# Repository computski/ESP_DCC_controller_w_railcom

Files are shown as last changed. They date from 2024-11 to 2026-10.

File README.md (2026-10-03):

# ESP_DCC_controller_w_railcom
PRODUCTION 2026-10-03. ESP 8266 DCC controller with railcom support. Uses most of the codebase from the ESP_DCC_controller project, but this project additionally supports a railcom cutout on the controller i.e. takes both X and Y to ground (or both 12v) during a railcom cutout slot that appears after every loco packet sent to line.   A railcom decoder will assert its data during the railcom cutout, and this is detected by dedicated hardware based around an LM319.  This data is fed to the ESP hardware UART and is gated-in during the cutout period via a railcom sync signal to a 6n317 opto isolator.  The UART operates at 250kbs.  I have designed a custom PCB for this project.

Now moved to ArduinoJson v7.0.4
Now uses ESPAsyncWebserver

https://arduinojson.org/news/2024/01/03/arduinojson-7/

Note: RX pin input is idle high.   The same is true of the comparator, i.e. active is a low signal

The railcom detector is integrated into the controller.  It uses an adaptation of the reference circuit in NRMA doc s-9.3.2_2012.   This is a floating earth detector based on the LM319.  The LM319 can operate from 
a split power rail, which means it does not use the negative rail to drive the opto LED current, instead driving the LED from the +ve rail and into the floating earth.  The LM319 is also faster than the LM393.
A high speed (10Mbd) 6N137 opto isolator is used to level shift between the floating earth and the RX input on the ESP mini, and is also used as a gate-in filter.
The 6N137 has an open collector output buffer and this is ideal as we can wire-OR this into the RX pin along with the on-board ESP mini USB-serial circuitry; this has an on-board 400R pull up.

The 6N137 also has a gating input on the output stage, and we drive this from railcom sync which is active high during the cutout.  This greatly cuts down on junk data into the UART and reduces software workload.

2025-05-13 fixed a bug in global.h which incorrectly defined the drive pins for the 2-pin drive arrangement on the LMD18200.  Railcom detector now works properly and with loco facing in either direction.

2026-02-19 LocoNet working, added support for OPC_IMM dcc immediate messages which allows use of multi aspect signals

2026-04-05 LocoNet bidirectional messages to Panel Pro working, additionally support for ESPACC accessory controller on the WiThrottle port

2026-10-03 final fixes to revised html pages in data

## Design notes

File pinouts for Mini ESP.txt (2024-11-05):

GPIO16 D0 jog SW (pcb pull down)
GPIO5  D1 Jog CK (pcb pull up)
GPIO4  D2 Jog DT (pcb pull up)
GPIO0  D3 SDA
GPIO2  D4 SCL
GPIO14 D5 IN2 IN4 LMD-DIR
GPIO12 D6 IN1 IN3 
GPIO13 D7 ENA+B LMD-PWM
GPIO15 D8 to JP2 presumably eStop to gnd
A0 goes to sense
GPIO3 RX

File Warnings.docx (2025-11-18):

Quick Start guide

DCC ESP with Railcom POM-read

Thank you for your purchase. This board is an updated version of the Instructables project found here https://www.instructables.com/member/Computski/

Specifically, this project https://www.instructables.com/ESP8266-DCC-Controller/

For support you can ask questions on the Instructables site or email me at computski@gmail.com

CAUTION: Please double check you have the correct polarity when connecting up the 12V DC supply. The board is not reverse polarity protected and you could damage it.

Your board is fully built, programmed and tested. Just connect 12v DC power and X-Y connections to the track and you are ready to run DCC locomotives via Engine Driver on an Android phone.

The board is capable of supporting an LCD display, 16 key keypad and a jogwheel acting as an optional local hardware interface. See the Instructable for more details.

The board can handle a max of 4 Amps, however, the current trip threshold is set to 1 Amp by default. You can change this through the hardware screen on the web interface, or through the hardware screen under the DCC ESP settings found in the Engine Driver app on your phone.

You can also feed the unit with a higher DC voltage, say 14V if you want a higher track voltage, but note the controller has an over-voltage trip which is set to 15V by default. You can change this in the hardware screen.

I also enclose a revised user guide, and can email you a copy of this on request.

Happy railroading!

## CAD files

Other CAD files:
1556CGY.dwg

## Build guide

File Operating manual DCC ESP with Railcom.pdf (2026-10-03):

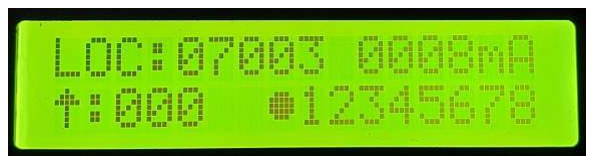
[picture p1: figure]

### 1 ESP DCC manual 2026-10-03

### ESP DCC controller. Operating manual rev 3 (boards with POM read and Loconet/ JMRI support)

PART ONE: For units equipped with Display, keyboard (DSKY) and jogwheel
The unit boots and shows the current software version as a date. It will then power up the track and enter loco operations mode.

Operations mode
Operate mode. Here you can control one locomotive at a time.
B-key will switch between locomotives
A-key will let you edit loco addresses, delete locos and also set 28/126 speed steps.
To select a loco from the existing roster, press B repeatedly. 8 locos are supported in the roster. Press A to enter edit mode. Press * to toggle between 3-digit loco addresses and 5-digit addresses. Press # to will toggle 28 and 126 step speed modes. If you enter a new address by using the digit keys, then press A, the unit will create a new loco entry in the loco roster.
The unit responds with “loco created.” If it successfully creates a new entry. If there are no loco slots left, and no older locos can be bumped, then you will see a “no slots” message. A loco can only be bumped if it is stationary and is not currently under WiThrottle control.
To delete a loco, enter 000 or 00000 as the address and press A. You will see a ‘loco deleted’ message.
Each time the loco roster is changed, it is saved to EEPROM and also broadcast to all WiThrottles. You may also abort your edit by pressing B. This will take you to loco operate mode.
In loco operate mode
*-key to increase speed
0-key to decease speed
*0 together will emergency stop that loco. #-key will reverse direction if speed is zero. D-key will toggle headlamp on/off aka F0. 1-9 keys will toggle F1 to F9

A-key will enter edit mode
B-key will select next loco/ abort edit C-key will toggle “shunter” mode

In operate mode, you can set the speed of one loco, then select another and set its speed and so on. The red emergency stop button comes in handy if you lose track of your locos and need to hit the panic button. The red emergency stop button will send eStop to all locos. It will not turn off track power.
Pressing C will toggle shunter mode. This is indicated by a solid arrow head for direction. In this mode, decreasing speed takes you down through zero, then direction is automatically reversed and

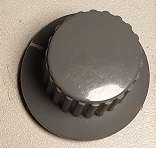
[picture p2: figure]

### 2 ESP DCC manual 2026-10-03

the speed will increase again. This is useful for shunting because it saves you having to enter a direction change command.
In operate mode you can also rotate the jogwheel CW or CCW to increase/decrease speed. If you press the jogwheel down, the loco will brake. Its speed will be reduced by 30% whilst you are holding the button down. Best used with an inertia setting on your decoder.

If the loco is stationary and you hold the jogwheel button down for more than 2 seconds, the loco direction is reversed.

When driving with 126 speed steps, you may fast-rotate the jogwheel to have it increase/decrease speed in 5 step increments/decrements.

If shunter mode is active, the loco speed can be decreased by rotating the jogwheel say CCW. Once the speed hits zero, the direction automatically reverses and continued rotation in the same CCW direction will now cause a speed increase in the new loco direction.
With these features it is possible to drive, brake and reverse the loco solely from the jogwheel. This is a useful feature which is carried over to the turnout display.

Turnout display
When in operations mode, press mode briefly and you are taken to turnout mode. If you press and hold mode, you are taken to POM mode.
The unit can store 8 turnouts in the turnout roster and these are kept in EEPROM. To call up a turnout, start typing its 2-digit address. E.g. 01. Once the second digit is entered, the cursor will jump to that particular turnout and blink on top of the closed/thrown indicator.

Pressing # will toggle the turnout state. Closed is indicated by a vertical line, thrown by a forward slash.
You can also quickly toggle turnouts in slots 1-4 by pressing the A, B, C or D button.
As you enter more turnouts, the least used ones are bumped. The unit supports addressing turnouts 01 to 99 through the keypad. It is possible to use the full 1 to 2047 turnout address range if you operate through the WiThrotttle. Addresses over 99 are shown in hex, and those over FF are shown as XX because they cannot be displayed in 2 digits.
Whilst in the turnout display, the jogwheel will still control the last selected locomotive. This makes shunting operations very easy. You may stay in the turnout display switching the turnouts and continue to drive a loco through the jogwheel.

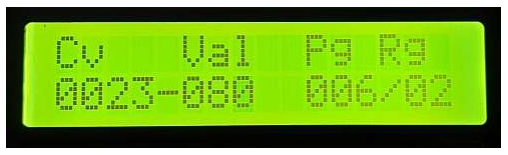
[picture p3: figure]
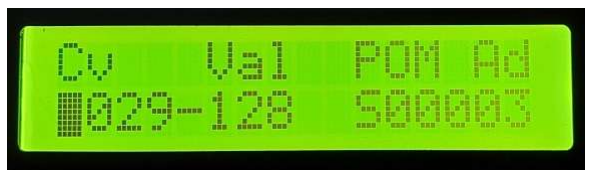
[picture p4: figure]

### 3 ESP DCC manual 2026-10-03

Service mode (programming track)
To enter Service Mode, hit the Emergency Stop button and briefly press the Mode button. # and * will move the cursor across the CV address and CV value.
A-key will read the CV.
B-key has no function.
C-key writes in page/register mode. D-key writes in direct mode.
When in Service mode, the unit complies with the DCC specification and will trip if the track current exceeds 250mA.
If you have just fitted a decoder to a loco, do not put it on the main track in operations mode! First put the unit into Service mode, this sets the power to max 250mA and then place the loco on the track. Try and read CV1. This should return a value of 3. You should also hear the loco buzz/move momentarily as it energises its motor as part of the read. If this does not happen, or the power trips at 250mA or more, then your decoder is not wired correctly and you must correct this before you put it on the main track in operations mode.
This unit only has one track output. There is no separate programming track. Also Service mode is a broadcast mode so all locomotives which receive the signal will be reprogrammed. There are many DCCwiki pages available on the details of service mode.
Only byte read and byte write are supported by the unit. Bitwise operations are not supported Enter a CV and hit the A-key to read that register. If it fails to read, it is possible your decoder is wired incorrectly, or the loco is off the track or its wheels/pickups are dirty.

Hit the mode-key to exit back to operations mode.
Note: the DCC specification does not allow for driving locos when in service mode, i.e. you cannot test the loco will move forward/backward within the 250mA power limit. However, if you can read CVs successfully, then it is safe to put the loco on the track in operations mode.

POM mode (programme on the main)
POM mode is entered by long-pressing mode when in the operations mode loco display. A-key will read the CV from the loco address¹
B-key toggles between byte mode (shown) and bit mode
C-key has no function
D-key writes to the loco address
# and * keys navigate the cursor

1
For revised hardware boards, rev 4 blue PCB with Railcom read support

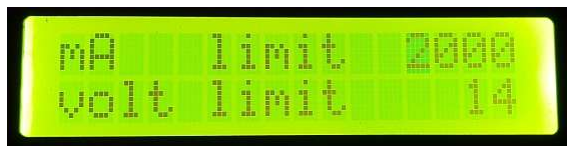
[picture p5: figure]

### 4 ESP DCC manual 2026-10-03

POM mode reads or writes to CV registers when the loco is on the main line in operations mode. You can even write certain decoder CVs whilst the loco is in motion. Short loco addresses are denoted by S, long loco addresses by L.
Bitwise mode. Here you can set or clear individual bits 0 to 7 in a specific CV register.

The loco will not visibly acknowledge the byte or bit write. The loco may acknowledge over LocoNet, which is not supported by this unit. For system boards that support Railcom read, pressing A will read the content of the CV to the display.
Setting current and voltage trip
Enter this mode by pressing emergency stop and then long-press on the mode button.
A-key selects mA limit.
B-key selects volt limit
Mode-key exits and writes new settings to EEprom.

PART TWO: Web interface
The unit supports a web interface and this is available even if the physical Display, Keyboard (DSKY) is not present.
- The default SSID is ESP_DCC, with no password.
- The default home page is http://192.168.6.1/index.htm
- You can also navigate to http://DCC_ESP.local as the unit supports mDNS

WIFI Station mode
The unit acts as a WiFi Station by default. In this mode, laptops and mobiles must find the SSID and connect to it.

WIFI Access point mode
Software versions 2025 onward. You can set the unit to connect to your home WiFi network, i.e. act as an access point. First connect to the unit in Station mode using a laptop or mobile, then can set the SSID and password for your network on the hardware screen. You enter these as the Station address and password. The next time the unit boots, it will try to log on to your home WiFi network as set in the Station parameters. If it succeeds, it will appear on your home network at the IP address your router assigns it. You should program your router to assign the MAC address to a fixed

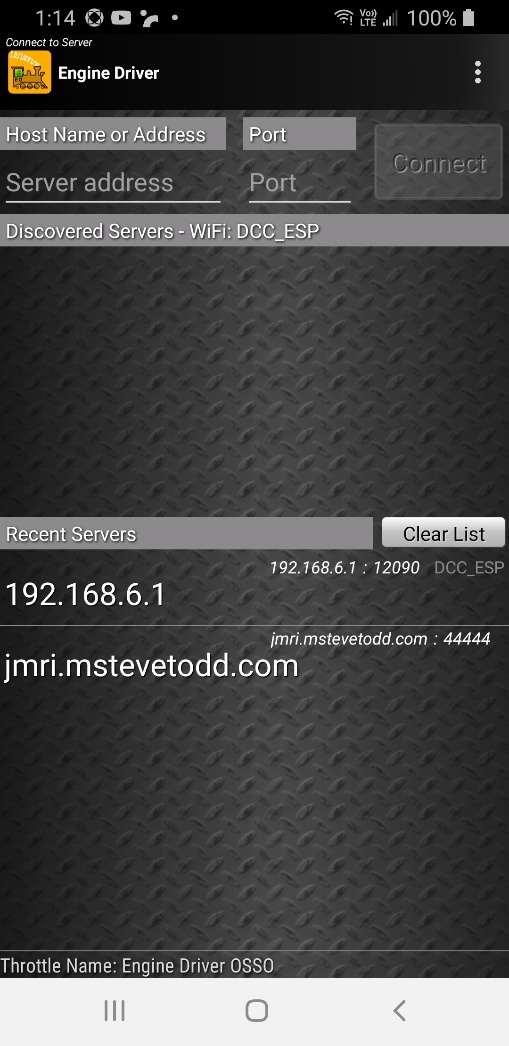
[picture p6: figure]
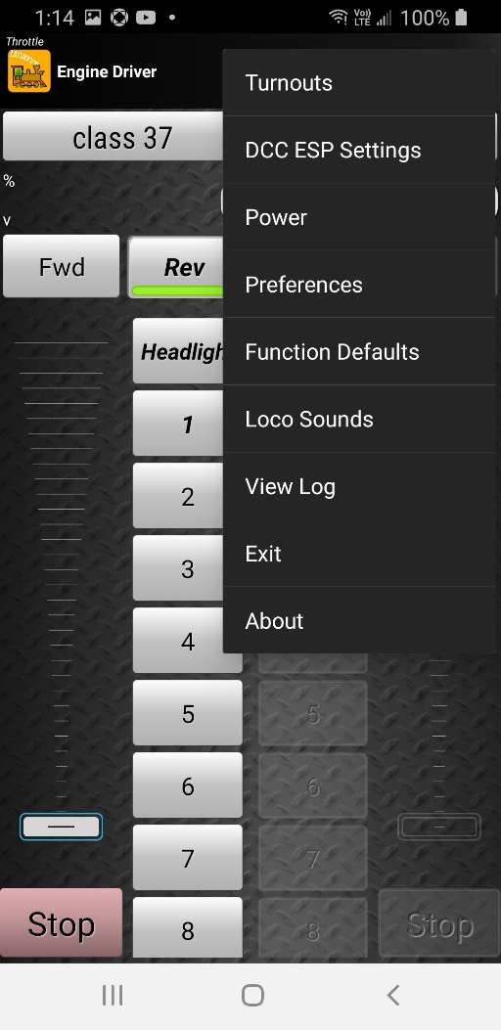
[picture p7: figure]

### 5 ESP DCC manual 2026-10-03

IP, and this way your devices such as phones running engine driver have a predictable known IP to connect to when on your home net.
If the unit cannot log onto your home network (e.g. your WiFi is down, you changed the SSID or password, you move house etc.) then the unit will boot in Station mode and appear as ESP_DCC. This lets you log back into the unit and update the Station settings.

Example: connect using Microsoft Edge on a laptop
Turn on the DCC controller, use laptop to search for ESP_DCC wifi SSID (no password). Open Microsoft Edge, enter http://192.168.6.1/index.htm as the URL and you should see the home screen below.
Example: connect using a mobile phone and Engine Driver.
Turn on the DCC controller, go into your phone’s WiFi settings and chose ESP_DCC. Then open Engine Driver (Android) and set the server address to 192.168.6.1 and port 12090, click on this in your phone and Engine Driver will connect to the DCC controller (left screen below)

Once connected, you can open the loco roster and select a loco. You can also click on the 3-dot menu top right, and select DCC ESP settings. Under this option you will find all the web menus described on the following pages. The menu options (right hand pic) are only available after Engine Driver is able to successfully connect to the server (i.e. to the ESP DCC controller). You enter the server details top of left hand screen, namely server address 192.168.6.1 and port 12090

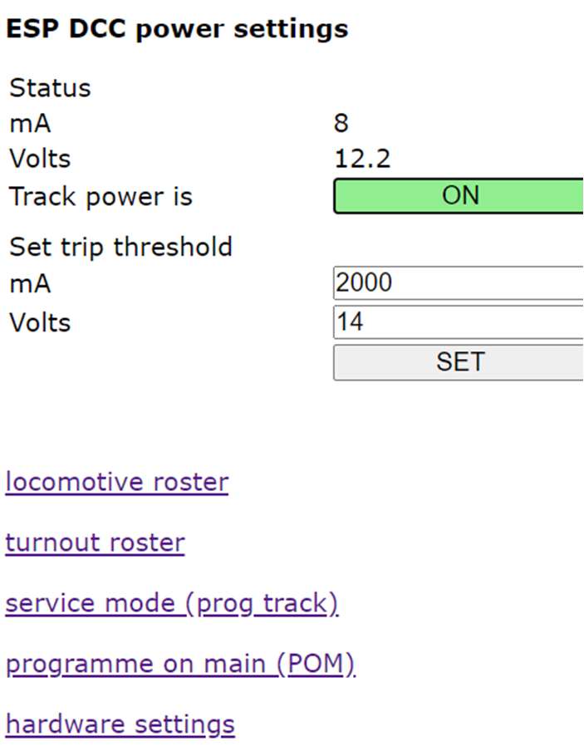
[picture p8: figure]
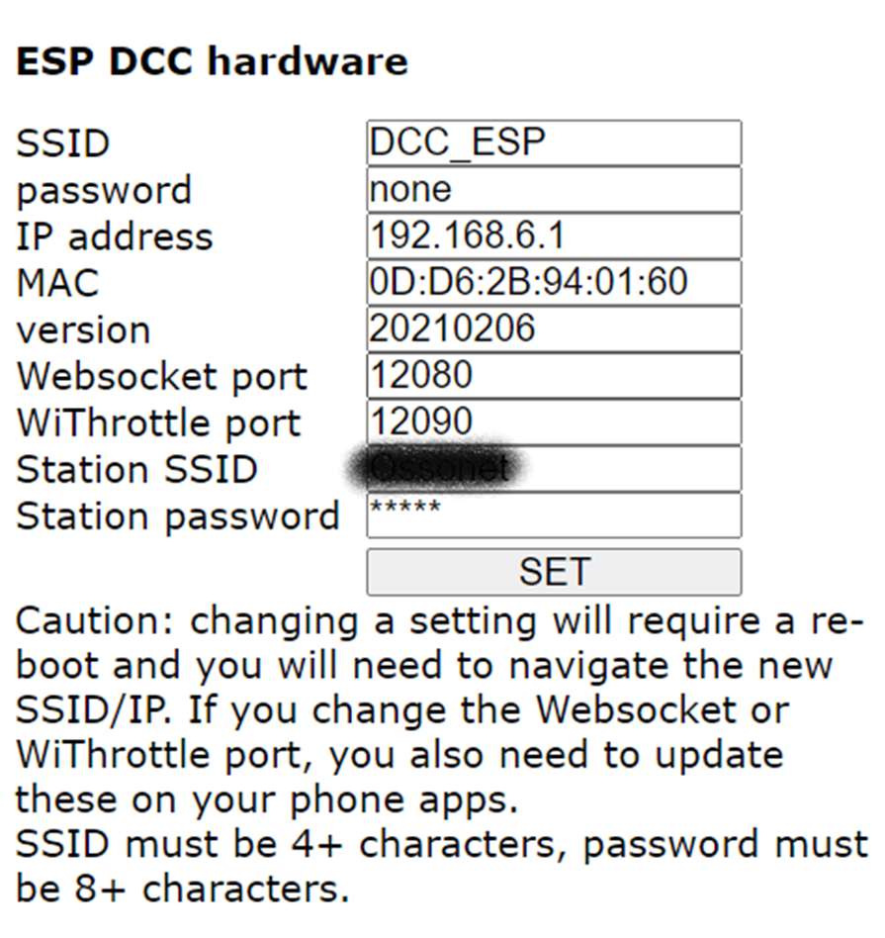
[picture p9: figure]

### 6 ESP DCC manual 2026-10-03

The index.htm page is the system home page and allows you to navigate to the other web pages.

On this page you can also turn track power on/off, and also set the current and voltage trip thresholds.

Live readings of actual track power and voltage are displayed on this page.

The hardware page allows you to set the SSID and set a password when unit acts as a standalone station.

The IP address can be set. The MAC is read only.

The WiThrottle port can be changed. WiThrottle(IOS) defaults to 12090 and cannot use ports below the 10000 range. EngineDriver can use any port, but 12090 is fine.

The websocket port is used for these web pages, and never needs to change. (not until this unit supports DigiTrains as a future).

Any changes you make here will require you to reboot the unit. And obviously if you change the SSID or IP address, you will need to navigate to your new settings.

2025: Station SSID and Station password are the network settings of your home network, should you wish to connect via this. Also the default WiThrottle port is now 2560.

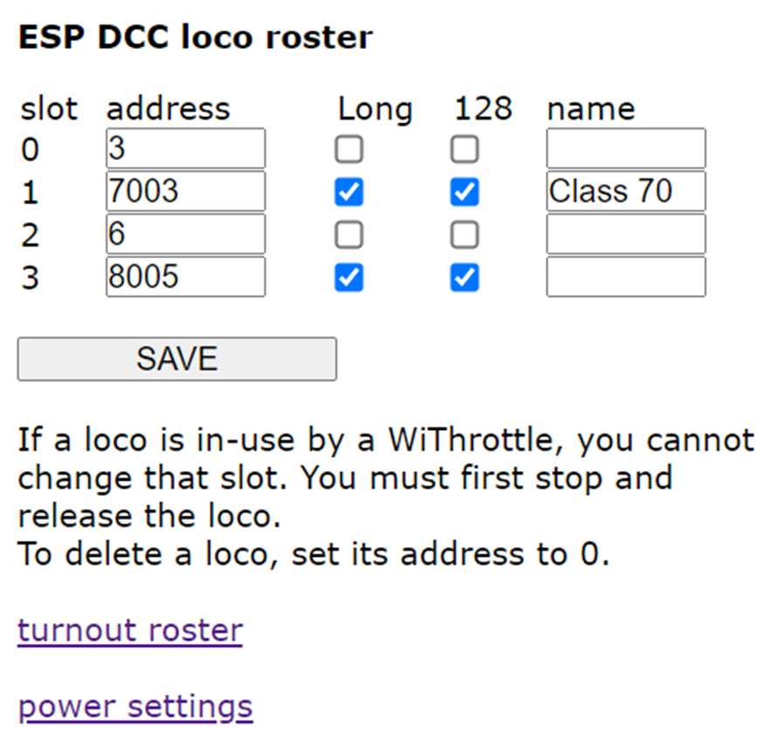
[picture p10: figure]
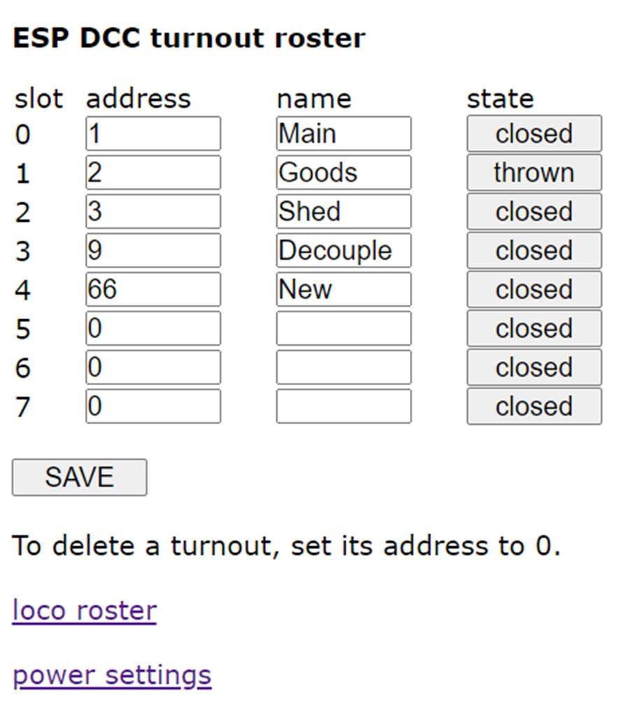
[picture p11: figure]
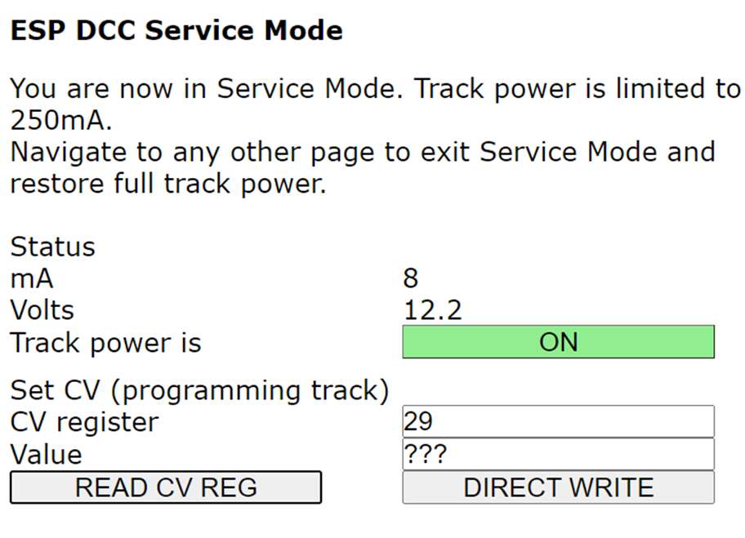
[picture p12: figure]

### 7 ESP DCC manual 2026-10-03

The loco roster can support up to 8 locos. You may edit the roster entry here, and these changes will flow through to any WiThrottle controls.

If a slot is in use, i.e. the loco is moving or it is under the control of a WiThrottle, then the entry is highlighted and you cannot edit it until you zero the speed and/or release the loco in WiThrottle.

There is no support for DCC defined consists. You can create ad-hoc consists in EngineDriver.

The turnout roster can hold 8 turnouts. Routes are not supported.

You can edit the turnout address and name. Changes are pushed through to the WiThrottles. You can also toggle the turnout states from this page.

Addresses of 1-2047 are supported. This is an 11-bit schema.

Note: The DCC specification defines a 9-bit turnout schema with each address supporting 4 devices. This is quite confusing and most manufacturers use the 11-bit schema where each device effectively has its own address. DCC++ uses a 9-bit schema.
Service Mode, aka programming track. When you enter this mode, power is limited to 250mA. You can read/write CVs.

Only direct write mode is supported, and only byte values can be read/written.

If you have installed a new decoder, do NOT put it on the track in operations mode. First set the unit on service mode, then put the loco on the track. If you can read/write CVs to it, then it is wired correctly and can be used on the main.
Important: you need to navigate away from this page to allow full power to be restored to the main.

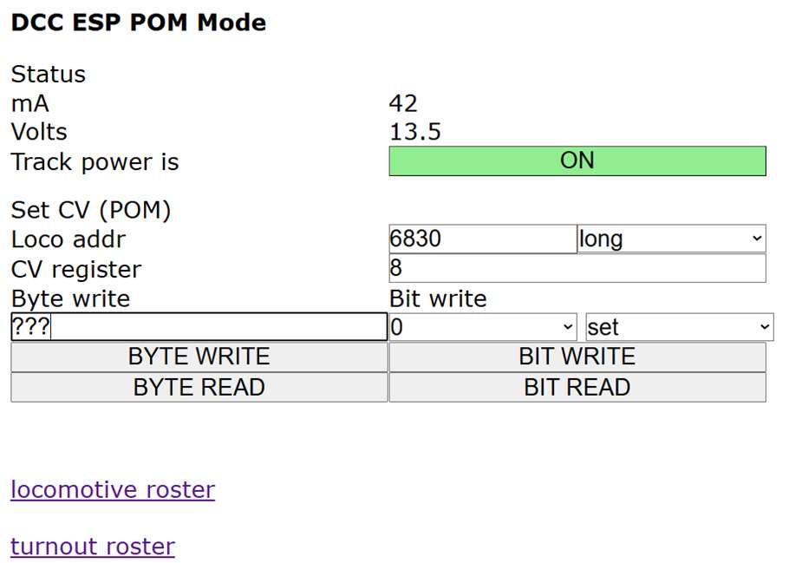
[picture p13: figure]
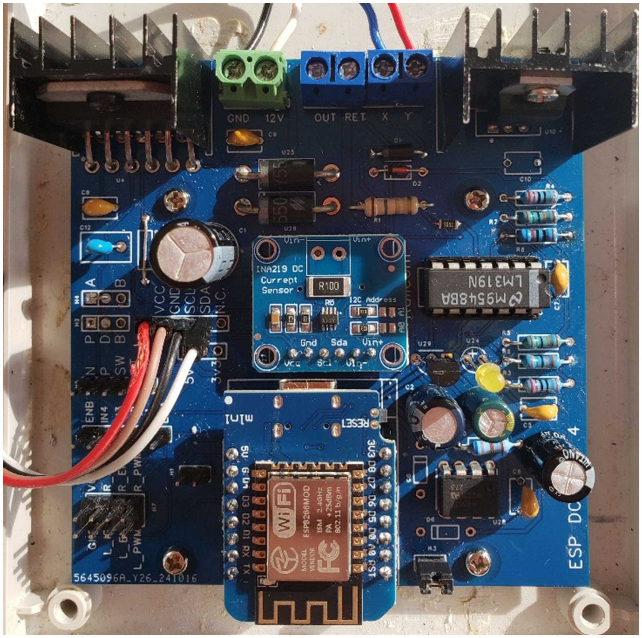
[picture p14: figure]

### 8 ESP DCC manual 2026-10-03

In POM mode, you can read/write to any loco address short or long on the main line. Some decoders even support you doing this as the loco is running.

2025: If using the rev 4 blue PCB which has Railcom read support, you can also read CVs from your locos.

You can bit write or byte write.

Railcom is not supported by all decoders, but is supported by many new decoders. This system does not support automatic discovery of locos on the main.

The 2025 rev4 board with Railcom read support.

Boards with software version 2025-08-xx and higher now support a jogwheel even when in WIFI only mode. If you do not fit an LCD display and keypad, you can still connect up a jogwheel and this will control the active loco as set in the “Jog” column in the DCC ESP Settings page, loco roster. The jogwheel is optional, and offers yet another way to control the speed of the loco. You will find that the loco is put into ‘shunter mode’, i.e. if you dial the speed down with the jogwheel, it will decrease through zero, cause a direction reverse and increase speed in the reverse direction.

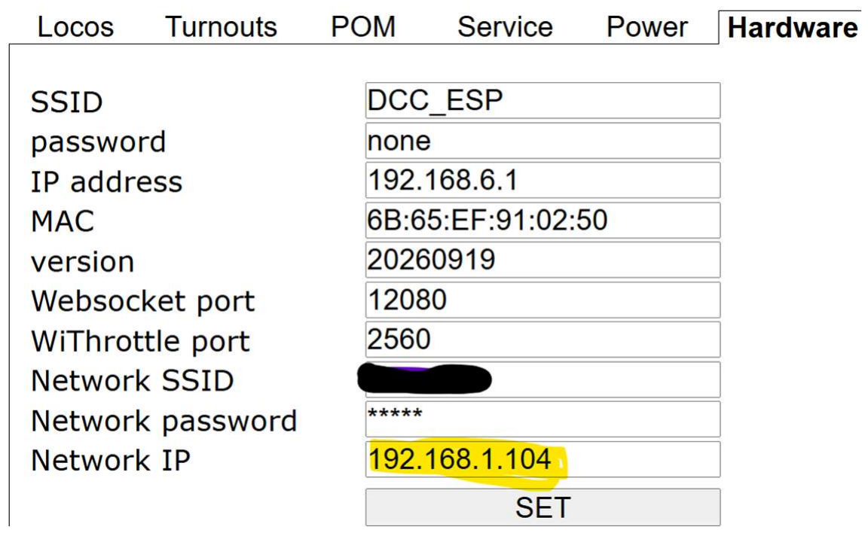
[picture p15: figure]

### 9 ESP DCC manual 2026-10-03

PART THREE: Interworking with JMRI Decoder Pro and Panel Pro
A new feature of the software in 2026 is support for JMRI and Loconet.
JMRI is an opensource and free model railroad control system that runs on a laptop. It has two main modules; Decoder Pro, which manages multiple loco decoder CV parameters (via Service Mode or POM) and Panel Pro, which manages multiple turnouts and sensors. Additionally, the JMRI system can support multiple WiThrottles such as Engine Driver. I believe it is also capable of automating operations on a layout. It is very powerful and rather complex but there are a lot of good tutorials on the internet that cover how to set it up and how it works. In this manual I will only cover the basics of how to connect the DCC_ESP to JMRI and run a few simple tests.

Connect to JMRI
Your laptop running JMRI must be able to connect to the DCC_ESP. It can do this via the DCC_ESP acting as an Access Point (aka local hotspot) or via the DCC_ESP first connecting to your home Wifi. To make life easier, the DCC_ESP supports mDNS which is a local domain name system, and this means the DCC_ESP appears at http://DCC_ESP.local (that is DCC_ESP.local) and you do not have to know its actual IP address.

Note that if the DCC_ESP fails to connect to your home WiFi after 20 seconds it will revert to acting as an Access Point and will appear as SSID DCC_ESP (unless you changed this name). This is useful if your router is turned off, you are at a friend’s house or changed your WiFi password.

If you need to discover what IP address your home router
assigned to DCC_ESP, you can navigate to http://DCC_ESP.local and check the hardware tab. The Network IP is set by your router.

Fire up JMRI Decoder Pro on your laptop and set its connection configuration. The DCC_ESP emulates a Digitrax DCS240 running Loconet over TCP IP on the WiThrottle port number (2560 in example above) and the Network IP (or DCC_ESP.local which saves you having to know the IP).

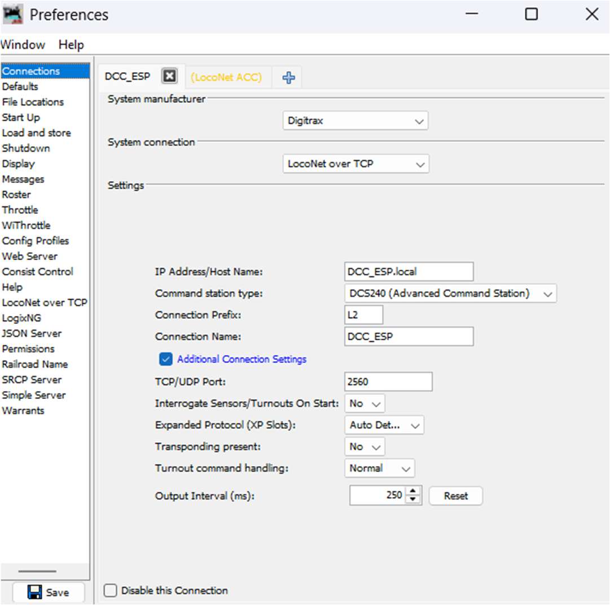
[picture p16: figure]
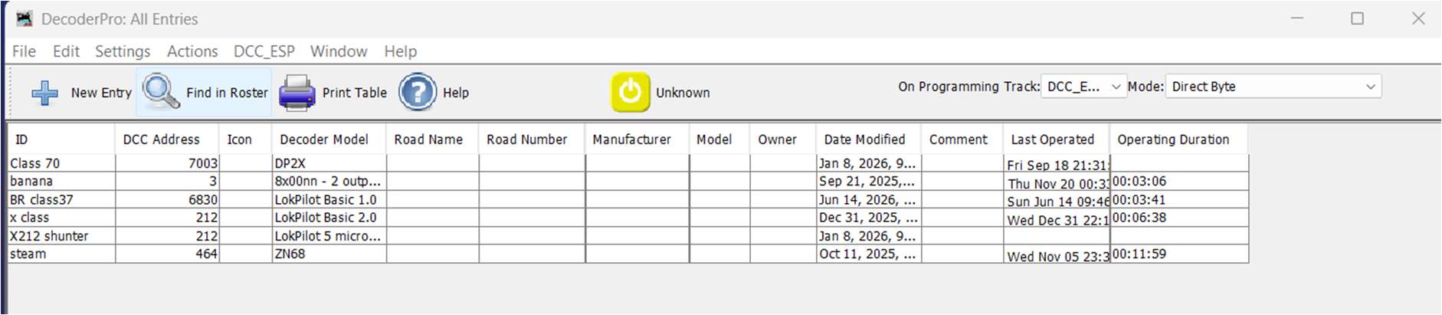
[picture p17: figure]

### 10 ESP DCC manual 2026-10-03

In JMRI preferences… connections… Select Digitrax
LocoNet over TCP

then
DCC_ESP.local (or the network IP address)
DCS240
The TCP port is 2560 or whichever port you set as the WiThrottle port on the DCC_ESP

And chose SAVE. The DCC_ESP emulates a Digitrax DCS240 controller and runs Loconet.

If Decoder Pro finds the DCC_ESP, it will connect and show you its current locomotive roster. You will also see one of the menu options appear as DCC_ESP. Note that Decoder Pro can hold hundreds of locomotives in its roster, you are not limited by the 8 loco limit in the DCC_ESP EEPROM. (You are limited to controlling max 8 locos simultaneously). Also note the Decoder Pro loco roster is NOT pulled from the DCC_ESP. The roster is set up by you, directly in Decoder Pro and is entirely separate to whatever roster happens to be in the DCC_ESP.

If you invoke the ECC_ESP menu item and select Monitor LocoNet, you can see the LocoNet messages sent to/from the DCC_ESP in a pop-up window. For example if you toggle the power button (where it says Unknown above) then you will see this…

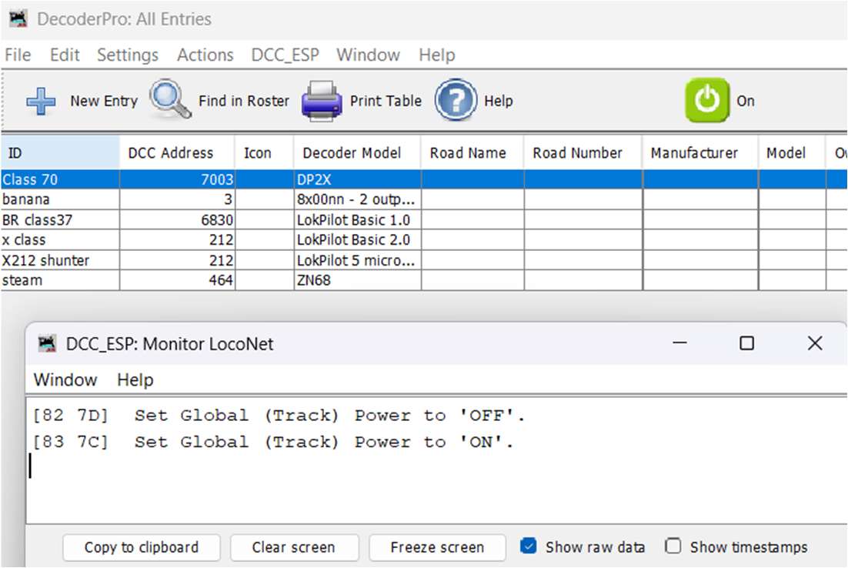
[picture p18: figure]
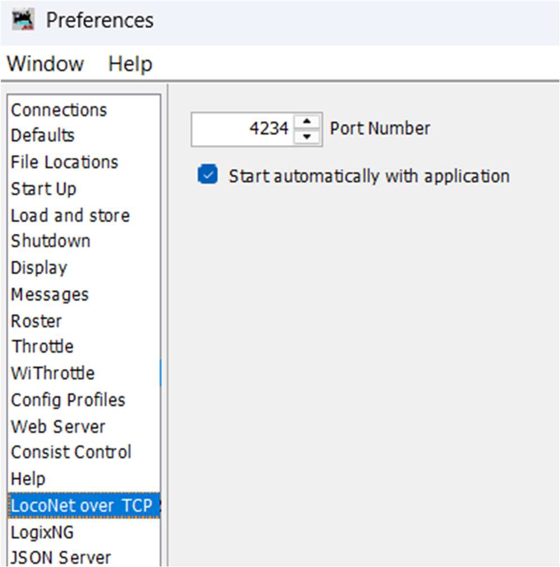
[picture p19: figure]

### 11 ESP DCC manual 2026-10-03

Toggling the power button will send a Global Track power message over LocoNet to the DCC_ESP. You will see the trackpower on the DCC_ESP go off/on (as indicated by the yellow LED)

In Decoder Pro, Edit… Preferences… select LocoNet over TCP and set the port to 4234 and to start automatically.

This is required to communicate with ACC_ESP accessory controllers, see a future Instructables.

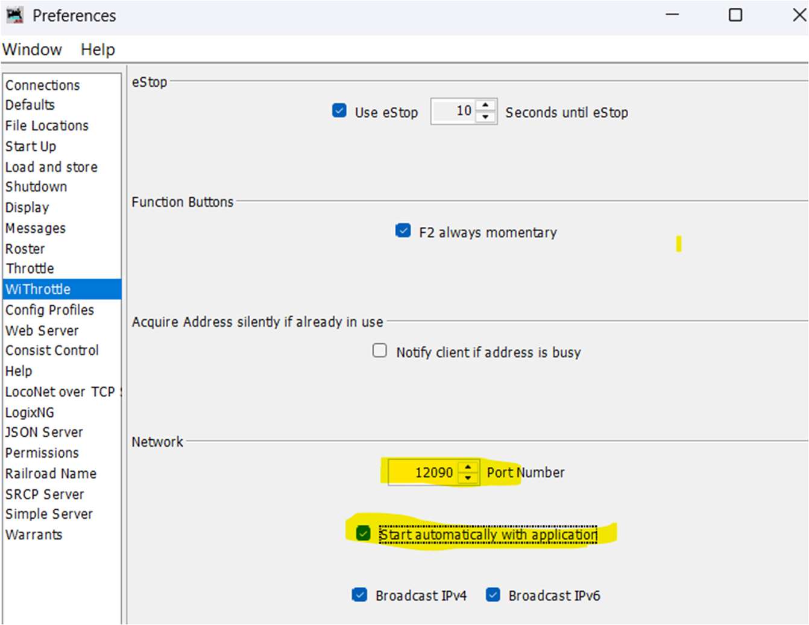
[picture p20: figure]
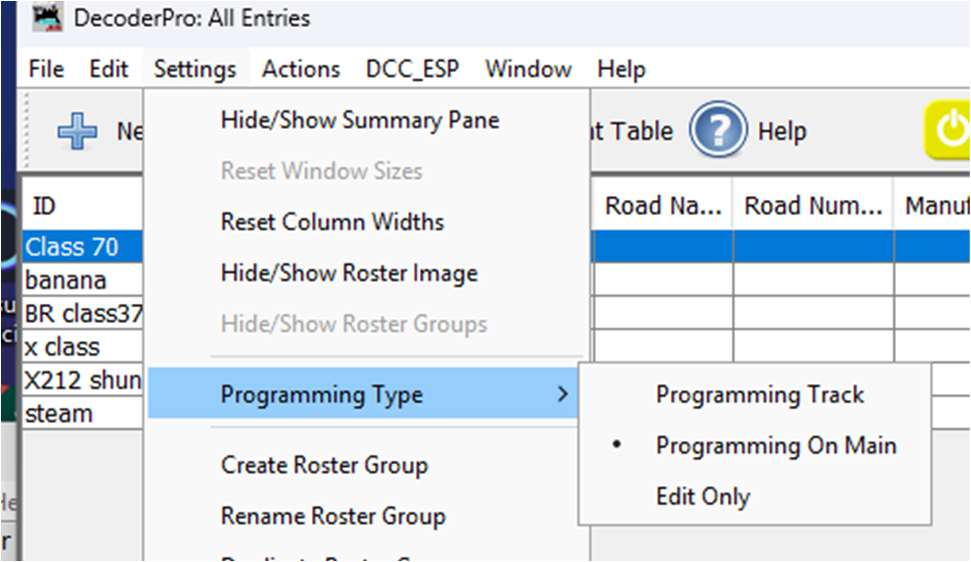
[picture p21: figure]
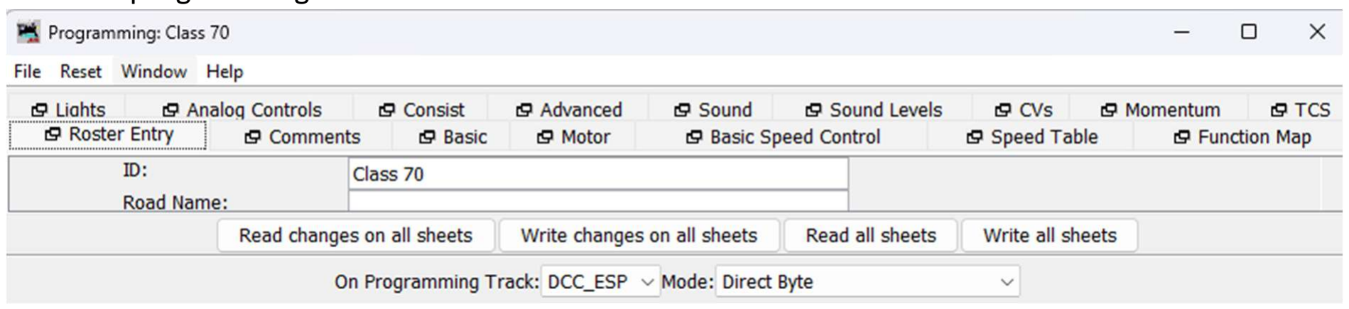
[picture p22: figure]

### 12 ESP DCC manual 2026-10-03

And, also configure
WiThrottle to start
automatically on port
12090.

This is used by Engine
Driver throttles. These
need to connect to
JMRI on the laptop and
NOT connect directly to
the DCC_ESP (because
it is not operating as a
stand alone device).

Reading/ writing loco CVs
In decoder pro you need to set whether you wish to use POM or Service Mode when reading/writing CVs. This is controlled from Settings… Programming Type…

If you select Programming Track (aka Service Mode) you will find that you can read/write “sheets” from the programming window.

Note: sending Programming Track commands to the DCC_ESP controller will put it into low power 250mA mode (aka Service Mode). To exit this mode, you need to close the programming window and then cycle the track power off-on. You cannot drive a loco during Service Mode. This is by-design and part of the DCC specification.

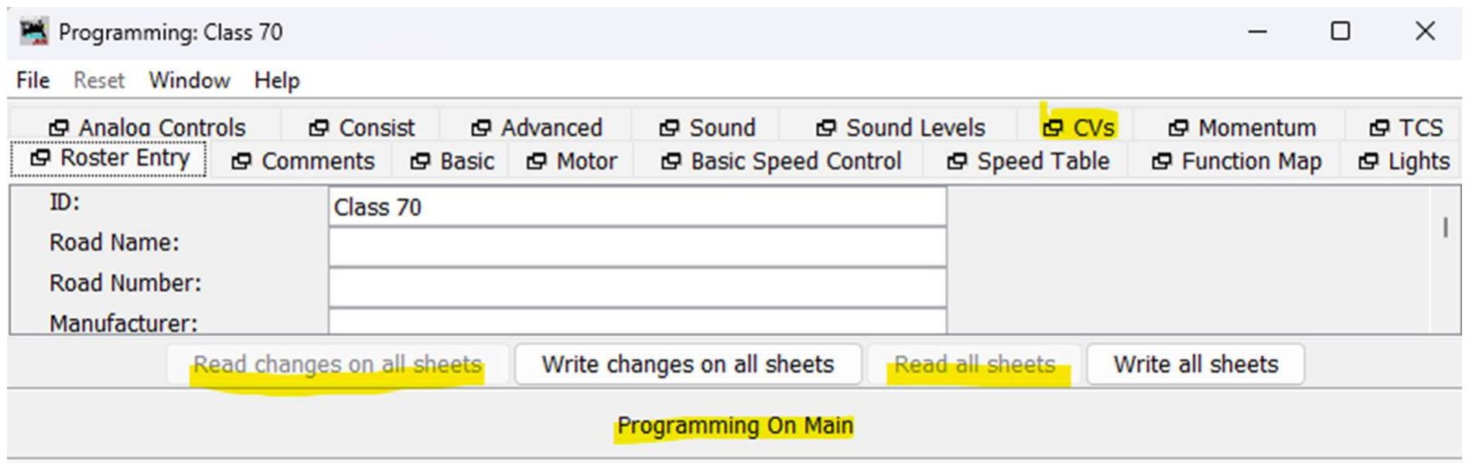
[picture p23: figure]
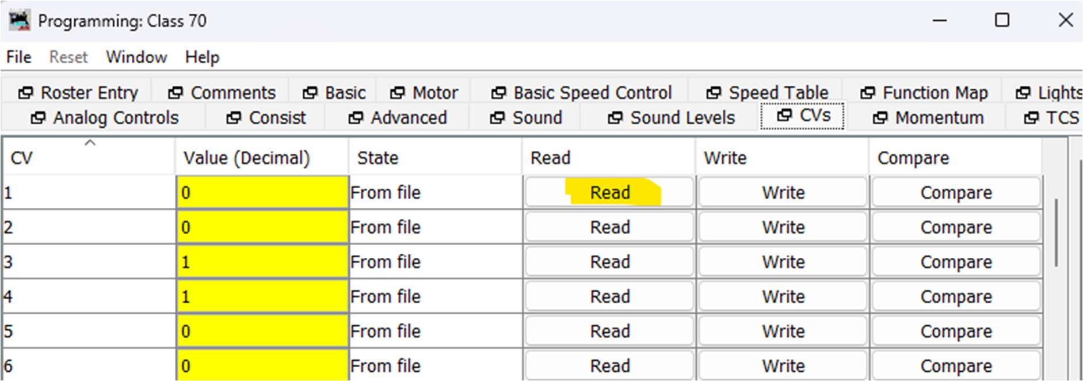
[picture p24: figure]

### 13 ESP DCC manual 2026-10-03

If you select Programming on Main, you will find that you can only write “sheets”. This is a limitation / oversight of the JMRI software. It should provide a means to read all sheets via the Railcom protocol. Perhaps this will be addressed in a future release.

The workaround is to select the CVs tab, and manually click Read for each CV in turn.

- End -

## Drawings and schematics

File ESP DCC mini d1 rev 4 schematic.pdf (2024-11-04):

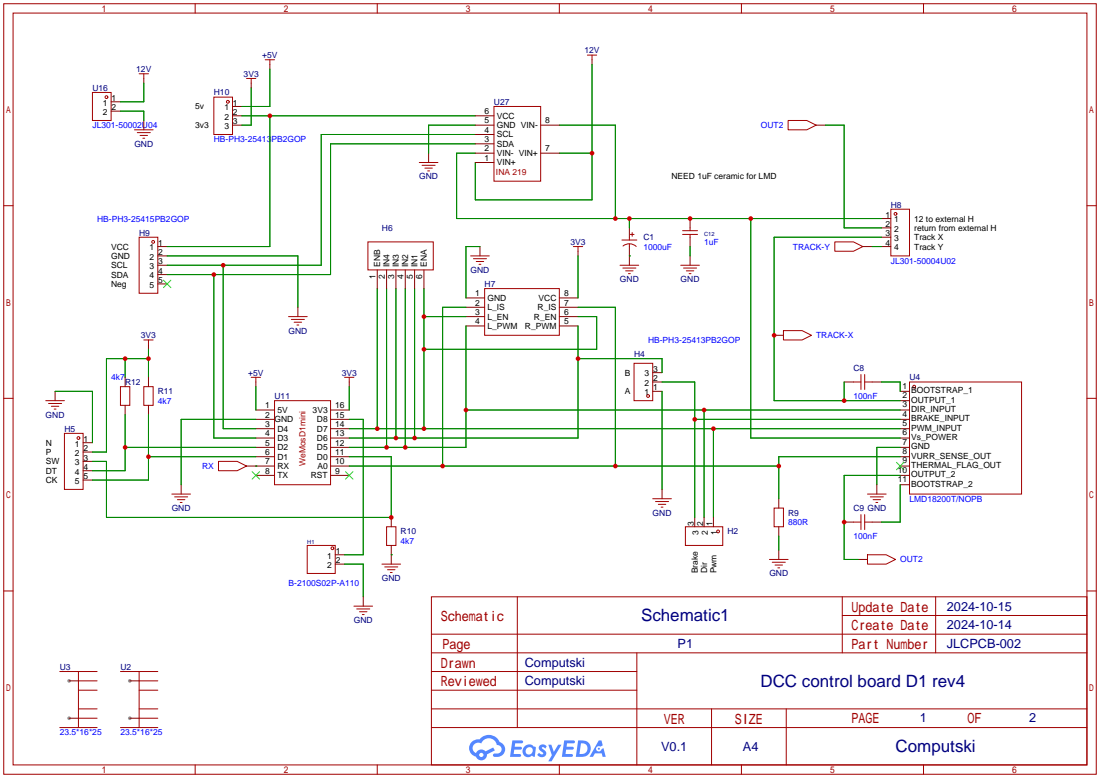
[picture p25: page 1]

NEED 1uF ceramic for LMD

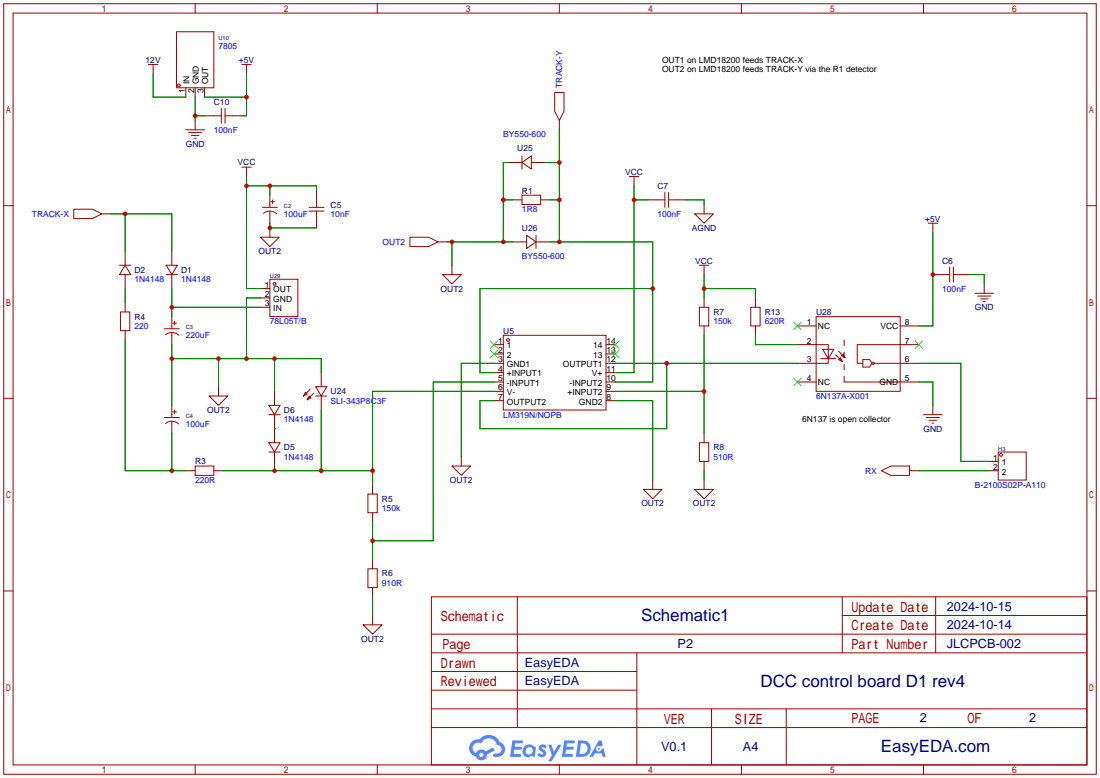
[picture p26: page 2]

OUT1 on LMD18200 feeds TRACK-X
OUT2 on LMD18200 feeds TRACK-Y via the R1 detector

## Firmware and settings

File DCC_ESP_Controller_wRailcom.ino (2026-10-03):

/*
	Name:       ESP_DCC_Controller.ino
	updated:	2026-02-18
	Author:     Julian Ossowski
	Target:		WeMOS D1 (R1 or mini)
	Note:		This device is 4M flash with 1M using LittleFS. These hold the webserver files
				and must be uploaded separately via vMicro publish server feature.
				>>> IMPORTANT make sure you set the filesystem type to LittleFS <<<
	Serial:		default speed on the serial is 115200
	IDE:		vMicro inside MS Visual studio.  Should also compile in the Arduino IDE.

	Hardware note: the ESP is a 3v3 device, the 1602 LCD and its backpack can run on 5v, as can the INA current monitor.
	It is recommended to run the I2C bus as 5v.  The ESP inputs are 5v tolerant and will work with a 5v I2C bus.
	

 Important: Tested and works with these library versions
 Adafruit INA219 library 1.0.3 works
 2024-04-25 switch to ArduinoJSON library 7.0.4


 These libraries need to be downloaded and put in the arduino libraries folder
 ESPAsyncTCP  https://github.com/me-no-dev/ESPAsyncTCP
 NewLiquidCrystal https://github.com/marcmerlin/NewLiquidCrystal

 These can be loaded through the arduino library manager
 WebSockets
 Adafruit INA219
 ArduinoJson
*/



//To delete: commented includes, the IDE adds these but they are not required
//#include <splash.h>
//#include <Adafruit_SSD1306.h> //added 2024-11-26 for latest adafruit INA support
//#include <Adafruit_NeoPixel.h> //added 2024-11-26 for latest adafruit INA support
//#include <WebSockets.h>
//#include <WebSockets4WebServer.h>
//#include <WebSocketsClient.h>
//#include <WebSocketsServer.h>
//#include <WebSocketsVersion.h>
//#include <ArduinoJson.h>
//#include <ArduinoJson.hpp>
#include <Wire.h>
#include "Global.h"
#include "DCCcore.h"
#include "DCClayer1.h"
#include "DCCweb.h"
#include "WiThrottle.h"
#include "LocoNetprocessor.h" 


//PIN ASSIGNMENTS - see global.h
//found that NMI in DCClayer1 conflicts with the WSP826WebServer. 
//Had to switch to regular ints.  There is no conflict with Websockets

uint8_t secCount;

void setup() {
	Serial.begin(115200);

	//Note: set the CPU clock freq to 160 in the IDE rather than using this dynamic update line
	//system_update_cpu_freq(160);
	Serial.println(F("\n\nBoot DCC ESP"));
	trace(
		Serial.println(F("trace enabled"));
		_Pragma("GCC warning \" TRACE IS ENABLED\"")
			)
		//2021-10-19 the unit can operate in DCC mode, or in DC mode pwm which supports a single loco, loco 3 with 28 speed steps
		//enable or disable the DC block as required in Global.h  DCC and DC are mutually exclusive


		

#ifdef	DC_PINS
//If DC_PINS is defined, this overrides DCC and we will create a DC system.  Entirel optional. If you want 
//a DCC system, then comment out or delete the DC_PINS definition in Global.h for the board you are using
DC_PINS

#elif defined DCC_PINS
//we expect to find DCC_PINS defined
DCC_PINS
#else
//need to define at least DCC_PINS, else we throw a compile time error.
#error "DCC_PINS or DC_PINS must be defined.  Neither is."
#endif


//restore settings from EEPROM
dccGetSettings();

//2025-08-15 now boot
DCCcoreBoot();

nsJogWheel::jogInit();

#ifdef _DCCWEB_h		
	nsDCCweb::startWebServices();
#endif

/*2024-08-28 start railcom protocol*/
railcomInit();


	/*2020-04-02 start WiThrottle protocol*/
#ifdef _WITHROTTLE_h
	nsWiThrottle::startThrottle();
#endif

	   


} //end boot




void loop() {

#ifdef _DCCWEB_h
	nsDCCweb::loopWebServices();   // constantly check for websocket events

	/*2020-05-03 new approach to broadcasting changes over all channels.
	A change can occur on any comms channel, might be WiThrottle, Websockets or the local hardware UI
	Flags are set in the loco and turnout objects to denote the need to broadcast.
	These flags are cleared by the local UI updater as the last in sequence*/

	nsDCCweb::broadcastChanges();
#endif


#ifdef _WITHROTTLE_h
	nsWiThrottle::broadcastChanges(false);
#endif

	//broadcast turnout changes to line and clear the flags
	updateLocalMachine();

	//call DCCcore once per loop. We no longer use the return value
	DCCcore();


	//2024-08-28 process incoming railcom data
	railcomLoop();



	if (quarterSecFlag) {
		/*isQuarterSecFlag will return true and also clear the flag*/
		quarterSecFlag = false;


		//2021-01-29 call processTimeout every 250mS to give better resolution over timeouts
#ifdef _WITHROTTLE_h
		nsWiThrottle::processTimeout();
#endif

		secCount++;
		if (secCount >= 8) {
			//measure 2 secs
			secCount = 0;
		
		
			//send power status out to web sockets
#ifdef _DCCWEB_h
			nsDCCweb::broadcastPower();
#endif


#ifdef _WITHROTTLE_h
			/*transmit power status to WiThrottles*/
			//2020-11-28 no need to do this so frequently
			//nsWiThrottle::broadcastWiPower();
#endif
		}//end one sec count


	}//qtr sec

}

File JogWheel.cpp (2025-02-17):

#include "Global.h"
#include "JogWheel.h"
#include <Arduino.h>

using namespace nsJogWheel;
/*JogWheel 2020-05-19
handles a rotary encoder, cheap mechanical type.  Software expects pushbutton to be active high, and jog1/2 to be active hi pulses

Some NodeMCU inputs have pull down or pull up resistors on them, most pins also have internal WPU.  
D0 (GPIO16) has a WPD instead. to preserve output state we need to access the low level registers

you cannot read the output latch unless the pin was previously declared as input_output.  Arduino
does not directly support this. easier to add pinState to the JOGWHEEL struct.  D0 here is used to monitor
pushbutton state.

Rotary encoder is a 2 output device moving from Step1 to Step2 and issues a quadrature code as it rotates.
These devices have lots of contact bounce.  The scheme is based around a state engine which is driven by the pin states
as sampled on change.  both pins have interrupt on change assigned to them.  The alternative is to constantly poll
the pins but this needs to be 5mS intervals or less.


 *   Position   Bit1   Bit2
 *   ----------------------
 *     Step1     0      0   start
 *      1/4      1      0   begin
 *      1/2      1      1   next 
 *      3/4      0      1   final
 *     Step2     0      0   start

 Gray code method.  Credit to site below
 http://www.buxtronix.net/2011/10/rotary-encoders-done-properly.html

 we attach an interrupt on CHANGE to both pins.  This method works reliably at any rotor speed and without the need
 to add capacitors as low pass filters.

 Hardware note: PIN_JOG2 already has a 12k pulldown on the NodeMCU board.  PIN_JOG1 has an external 12k pulldown added, and
 the pullup resistor is 1k.  The pushbutton is active high through a 1k pullup.

 BUG: if you change rotor direction, the first detent generates no output, second detent will generate an output in the new direction

2020-05-27 on 128 step mode, a full 6 rotations are required to traverse the range because there are 20 detents.  jog code now
measures time between detents and if this is short, sets jogHiSpeed flag which indicates the user is turning the knob
quickly.  main code acts on this by incr/dec in steps of 5 rather than 1.  This gives course/fine control.

2021-01-26 jogLoSpeed flag indicates if user is rotating slowly - approx two detents per sec, this is used to control
shoot through after a direction change in shunter mode

2022-01-07 modified code so that PIN_HEARTBEAT can be a pin other than GPIO16.  Strictly though, any jogwheel pushbutton 
whether a naked device or on its own PCM, should have a 1k series resistor on the switch, because the software assumes 
PIN_HEARTBEAT is always and output (used for LED drive) and will drive it high and low.  You want to avoid a direct short to
3v3 if the jog push button is held down.

One way to fix this is to define PIN_HEARTBEAT and PIN_JOG_PUSH as mutually exclusive, and jog push would always operate as input
active high, and the assumption is there are pulldowns on all jog lines.
*/



#ifndef ROTARY_HW40
//original generic rotary state engine, expects both switches open on each detent
#define R_START 0x0
#define R_CW_FINAL 0x1
#define R_CW_BEGIN 0x2
#define R_CW_NEXT 0x3
#define R_CCW_BEGIN 0x4
#define R_CCW_FINAL 0x5
#define R_CCW_NEXT 0x6
/*Values returned by the state engine*/
#define DIR_NONE 0x0  //not a complete step yet
#define DIR_CW 0x10  //clockwise step
#define DIR_CCW 0x20  //counter-clockwise step

const uint8_t ttable[7][4] = {
	{R_START,    R_CW_BEGIN,  R_CCW_BEGIN, R_START},// R_START
	{R_CW_NEXT,  R_START,     R_CW_FINAL,  R_START | DIR_CW},// R_CW_FINAL
	{R_CW_NEXT,  R_CW_BEGIN,  R_START,     R_START},	// R_CW_BEGIN
	{R_CW_NEXT,  R_CW_BEGIN,  R_CW_FINAL,  R_START},	// R_CW_NEXT
	{R_CCW_NEXT, R_START,     R_CCW_BEGIN, R_START},// R_CCW_BEGIN
	{R_CCW_NEXT, R_CCW_FINAL, R_START,     R_START | DIR_CCW},// R_CCW_FINAL
	{R_CCW_NEXT, R_CCW_FINAL, R_CCW_BEGIN, R_START},	// R_CCW_NEXT
};

#else
//HW40 type rotary, where switches alternate between both open and both closed at each detent
//Hardware bug.  if you use IO15 for one of the jog inputs, the rotary can sit with both high and this prevents boot :-(

#define R_START0 0x0
#define R_CW_BEGIN0 0x1
#define R_CCW_BEGIN0 0x2
#define R_START1 0x3
#define R_CW_BEGIN1 0x4
#define R_CCW_BEGIN1 0x5
#define R_UNKNOWN 0x6


/*Values returned by the state engine*/
#define DIR_NONE 0x0  //not a complete step yet
#define DIR_CW 0x10  //clockwise step
#define DIR_CCW 0x20  //counter-clockwise step

//at startup we don't know whether we are in start1 or start0, however after the user first rotates the wheel
//the code will synchronise to the wheel state

const uint8_t ttable[7][4] = {
	{R_START0,    R_CW_BEGIN0,  R_CCW_BEGIN0, R_START0}, // R_START0
	{R_START1 | DIR_CW,  R_CW_BEGIN0,  R_CW_BEGIN0,     R_START0  }, // R_CW_BEGIN0
	{R_START1 | DIR_CCW ,  R_CCW_BEGIN0,  R_CCW_BEGIN0,    R_START0  }, // R_CCW_BEGIN0

	{R_START1,    R_CCW_BEGIN1,  R_CW_BEGIN1, R_START1}, // R_START1
	{R_START1,  R_CW_BEGIN1,  R_CW_BEGIN1,     R_START0 | DIR_CW }, // R_CW_BEGIN1
	{R_START1,  R_CCW_BEGIN1,  R_CCW_BEGIN1,   R_START0 |DIR_CCW  }, // R_CCW_BEGIN1

	{R_START1,  R_UNKNOWN,  R_UNKNOWN,    R_START0  }, // R_UNKNOWN

};

//unknown is the boot state, however we only get our first read of the pins after an int.  so we still miss the first rotation
//what we need to do is sample the pins on boot and set START0/1 as required.

#endif

void nsJogWheel::jogInit(){
#if (PIN_JOG1==16) || (PIN_JOG2==16)
#error "jogInit: ERROR, you cannot attach interrupts to GPIO16"
#endif

pinMode(PIN_JOG1, INPUT); 
pinMode(PIN_JOG2, INPUT); 
attachInterrupt(digitalPinToInterrupt(PIN_JOG1), jogHandler,CHANGE);
attachInterrupt(digitalPinToInterrupt(PIN_JOG2), jogHandler,CHANGE);



#ifdef PIN_JOG_PUSH
//2022-01-07 if we only want a jog button, not a dual purpose line with an LED indicator on it, then define PIN_JOG_PUSH
//and if the pin happens to be IO16 then apply WPD to it; this is the only pin that supports WPD
pinMode(PIN_JOG_PUSH, INPUT);
#if (PIN_JOG_PUSH==16) 
pinMode(16, INPUT_PULLDOWN_16);
#endif

#elif defined(PIN_HEARTBEAT)
//dual purpose pin, LED heartbeat indicator (active low) and also acts as jogwheel pushbutton (active hi)
pinMode(PIN_HEARTBEAT, OUTPUT);
#endif

#ifdef R_START
jogWheel.state= R_START;
#else
jogWheel.state = R_UNKNOWN;
#endif
}
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

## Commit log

2024-04-25 Uses ArduinoJson v7
2024-11-04 The hardware schematic
2025-02-19 Add files via upload
    fixed WiThrottle to correctly invoke DCC ESP Settings menu item on Engine Driver
    [DCCcore.h, DCClayer1.cpp, Global.h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]
2026-04-04 partial refactor, bidirectional relay msgs working
